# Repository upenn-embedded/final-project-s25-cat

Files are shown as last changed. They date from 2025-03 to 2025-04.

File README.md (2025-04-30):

   Review Assignment Due Date (https://classroom.github.com/a/WXeqVgks)

# final-project-skeleton

* Team Number: 1
* Team Name: CAT
* Team Members: Chekayli Meyer, Andrea González, Taarana Jammula
* GitHub Repository URL: [upenn-embedded/final-project-s25-cat: ese3500s25-final-project-s25-final-project-skeleton created by GitHub Classroom](https://github.com/upenn-embedded/final-project-s25-cat)
* GitHub Pages Website URL: https://upenn-embedded.github.io/final-project-s25-cat/

## Final Project Proposal

### 1. Abstract

*In a few sentences, describe your final project.*

Our final project involves developing an autonomous trash collection vehicle that detects, collects, and stores small lightweight objects while navigating its environment. The robot moves forward until an object is detected within a few centimeters, at which point it stops, collects using a shovel-like part, and pushes it against a wall. The system would use an IR sensor for object detection and an ultrasonic sensor for wall detection.

### 2. Motivation

*What is the problem that you are trying to solve? Why is this project interesting? What is the intended purpose?*

We want to address the growing need for small-scale automated cleanup solutions in both indoor and outdoor environments. We are particularly interested in applying embedded systems and robotics principles to create a functional and modular trash-collection vehicle. This project will allow us to integrate course topics such as sensors, actuator control, serial communication, and embedded C programming in a hands-on and practical setting. Beyond the course requirements, we aim to continue building the system with real-time object recognition and autonomous navigation to explore more advanced robotics applications.

### 3. System Block Diagram

*Show your high level design, as done in WS1 and WS2. What are the critical components in your system? How do they communicate (I2C?, interrupts, ADC, etc.)? What power regulation do you need?*

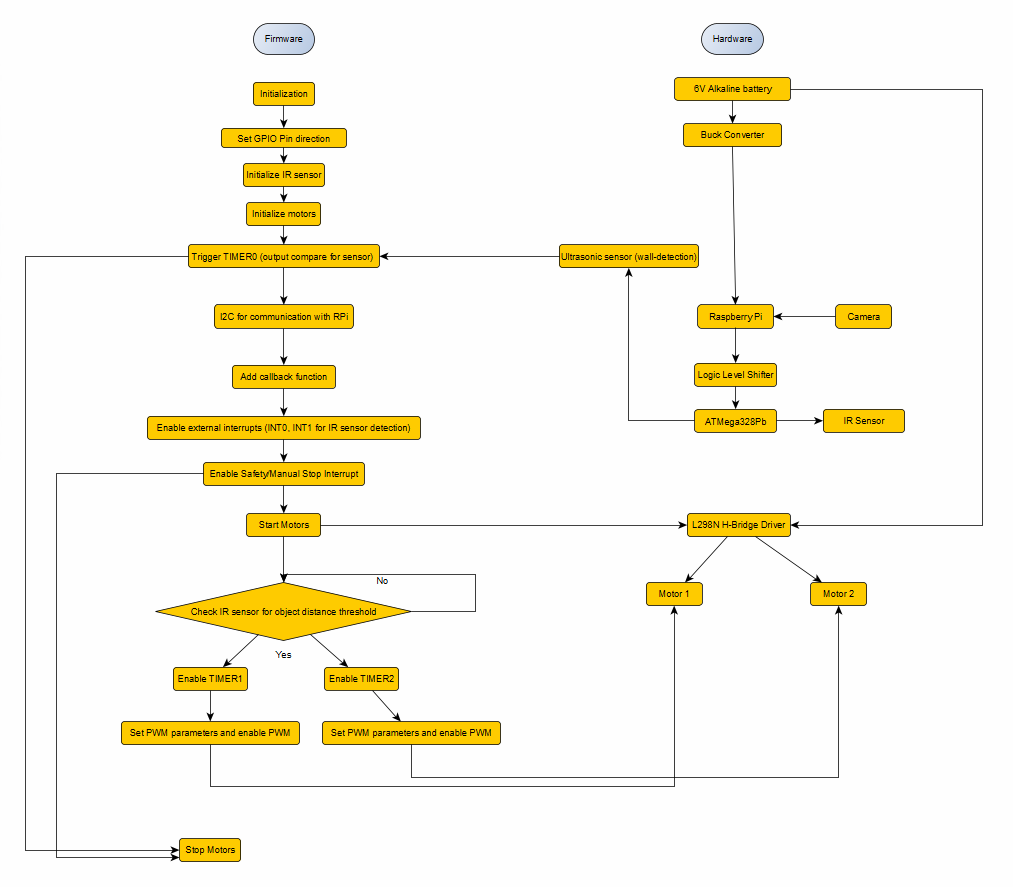
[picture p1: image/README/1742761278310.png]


The critical components of our system are the battery, buck converter, ultrasonic sensor, IR sensor, Raspberry Pi, camera, the ATMega328Pb, the L298N H-Bridge Driver, and 2 motors. The camera will be connected to the raspberry pi and will send information to the ATMega328Pb via I2C (serial communication). Timer0 will use output compare to detect walls, and Timer1 and Timer2 will be connected to separate motors once an object is detected (to push the object to the beacon). Interrupts INT0 and INT1 are used for IR sensor detection for the object. We also added a manual stop interrupt for safety. We have a buck converter from the 6V alkaline battery for power management to the raspberry pi. We also have a logic level shifter between the Raspberry Pi (3.3V) and ATMega328Pb (5V).

### 4. Design Sketches

*What will your project look like? Do you have any critical design features? Will you need any special manufacturing techniques to achieve your vision, like power tools, laser cutting, or 3D printing?*

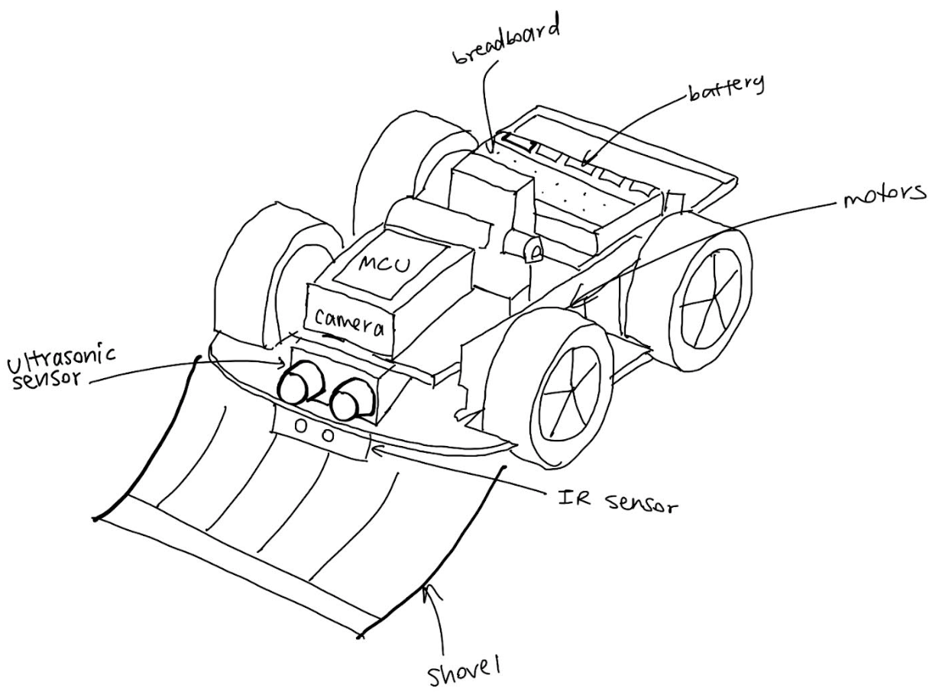
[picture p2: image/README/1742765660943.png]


We are lasercutting the base of the robot car and are purchasing the wheels and other required sensors. The critical design features like motors, a MCU stand, the battery, breadboard, IR sensor, ultrasonic sensor, camera, and shovel are included in the sketch above.

### 5. Software Requirements Specification (SRS)

*Formulate key software requirements here. Think deeply on the design: What must your device do? How will you measure this during validation testing? Create 4 to 8 critical system requirements.*

**5.1 Definitions, Abbreviations**

**ATmega328PB:** Microchip ATmega328PB microcontroller which is an 8-bit AVR MCU

**IR:** Infrared which is the proximity or reflectance sensor

**US:** Ultrasonic Sensor which will be used for distance measurement like in Lab 3

**PWM:** Pulse Width Modulation for motor speed control

**ADC:** Analog-to-Digital Converter

**I2C:** Inter-Integrated Circuit for two-wire serial communication protocol

**GPIO:** General Purpose Input/Output

**5.2 Functionality**

| **Req ID** | **Software Requirement** | **Verification Method** |
| --- | --- | --- |
| **SRS-01** | Sensor Polling Frequency: The firmware will poll the IR sensor and ultrasonic sensor at least 10 times per second (≥10 Hz each) to ensure timely detection of trash and obstacles. | Test: Use a logic analyzer or oscilloscope to verify sensor read operations (or an LED toggled in code on each read) occur at ≥10 Hz. Confirm that both IR and US sensor readings are updated at 100 ms intervals or faster under normal operation. |
| **SRS-02** | Trash Detection Threshold: The system will detect a piece of trash when the IR sensor’s reading exceeds a calibrated threshold value. Upon threshold crossing, the microcontroller shall initiate the trash collection routine (e.g. stop forward motion and activate the scoop) within 100 ms. | Test: Place a standard test object (simulated trash) at the detection range limit (e.g. ~15 cm in front of the IR sensor) and verify that the firmware recognizes it (IR reading above threshold) and triggers the scoop mechanism within 0.1 s. Repeat across several distances and object sizes to confirm reliable threshold detection. |
| **SRS-03** | Obstacle Avoidance Threshold: The firmware will use the ultrasonic sensor to detect walls or obstacles within a set distance (e.g. 30 cm). If an obstacle is closer than the threshold, the system shall halt or turn away within 100 ms to avoid collision. | Test: Gradually bring a wall or large object toward the robot and confirm that when it crosses the ~30 cm range, the robot’s motors stop or turn immediately (within 0.1 s). Use a measuring tape to ensure the trigger distance is ~30 cm and a timer or high-speed camera to measure response time from detection to motor stop. |
| **SRS-04** | Image Processing: The Raspberry Pi will capture images using an attached camera at a rate of at least 1 frame per second while scanning for trash or the beacon. It shall process the image and send detection results to the ATmega328PB via I2C within 500 ms. | Test: Place a target object (trash or beacon) in front of the camera. Verify that the Pi detects it and sends a message to the MCU in under 0.5 seconds. Check Pi logs and I2C communication timing. |
| **SRS-05** | PWM Motor Control Timing: The firmware will drive the motors using a PWM signal of at least 100 Hz frequency (with a target around 500 Hz for smooth control).The duty cycle shall be updated as needed (on speed changes) with a control loop period not greater than 100 ms. This ensures smooth speed variation without perceptible stalling or jitter. | Test: Measure the PWM output on the motor driver input using an oscilloscope. Verify the frequency is ≥100 Hz (e.g. ~500 Hz achieved, within ±5% of target). Change speed commands and confirm the duty cycle adjusts within the next 100 ms cycle. No audible irregularities or excessive motor vibration should be observed at the set frequency (confirm by listening and motor behavior). |
| **SRS-06** | I2C Communication Protocol: The microcontroller will communicate with the Raspberry Pi using the I2C bus operating at standard speed (100 kHz clock). Sensor status updates (e.g. trash detected, weight, obstacle distance) shall be transmitted to the Pi at least 2 times per second, and command/control data from the Pi (e.g. navigation commands) shall be processed within 100 ms of receipt. The I2C communication shall include error-checking (ACK/NACK monitoring); on a communication failure, the system shall retry the transmission at least once within 50 ms. | Test: Use a protocol analyzer or logic analyzer on the I2C lines (with level shifting in place) to verify the bus clock is ~100 kHz. Run the system and confirm via logs that sensor data messages are sent to the Pi ≥2 Hz. Introduce a forced NACK or bus error (e.g. by briefly disconnecting SDA) and ensure the firmware attempts a retry and recovers communication. All commands from the Pi (simulated via I2C commands) should be observed to take effect on the robot (e.g. a movement command causes motor PWM change) within 0.1 s. |
| **SRS-07** | User Interrupt & Safety Response: The system will provide a user interrupt (e.g. an emergency stop button or remote kill switch input to a GPIO interrupt). When the user interrupt is activated, the firmware shall immediately override normal operation and stop all motor activity within 100 ms, entering a safe idle state. Normal operation can only resume after a manual reset or explicit resume command. | Test: While the robot is moving, activate the emergency stop (press the button or trigger the interrupt line). Measure the time for the motors to stop (e.g. using timestamps or an LED triggered at stop); it should be <100 ms. Verify that during the stop condition, no motor motion occurs and the robot remains stationary. Attempt to issue movement commands during the stop state to ensure they are ignored. Finally, reset the interrupt and confirm the system only resumes operation when allowed. |

### 6. Hardware Requirements Specification (HRS)

*Formulate key hardware requirements here. Think deeply on the design: What must your device do? How will you measure this during validation testing? Create 4 to 8 critical system requirements.*

*These must be testable! See the Final Project Manual Appendix for details. Refer to the table below; replace these examples with your own.*

**6.1 Definitions, Abbreviations**

**H-Bridge** An electronic circuit (L298N module) that drives the motors in both directions

**Beacon:** Beacon used as a drop-off location marker

**Battery:** On-board power source (rechargeable) for motors and electronics

**6.2 Functionality**

| **Req ID** | **Hardware Requirement** | **Verification Method** |
| --- | --- | --- |
| **HRS-01** | Drive Motor Performance:The motor and drive system will propel the robot at a forward speed of≥0.3 m/son level ground while carrying a full load of collected trash (at least 2 kg). Each motor (with L298N driver) must provide sufficient torque to start moving from standstill with the full load and climb a mild incline of 5°. | Test: Load the robot with a dummy weight of 2 kg (to simulate trash). Mark a 1 m distance on flat floor and time the robot driving that distance; it should arrive in ≤3.3 s (0.3 m/s or faster). Verify the robot can also ascend a 5° ramp from standstill with the same load without stalling. Monitor motor current draw with an ammeter during these tests to ensure it stays within L298N and motor limits (no overheating or current limiting observed). |
| **HRS-02** | Infrared (IR) Sensor Range & Accuracy: The IR sensor will reliably detect a typical piece of trash (minimum size ~5 cm) at a distance of≥15 cm in front of the robot. Detection reliability at that range should be at least 90% (minimal missed detections under proper conditions). Beyond 15 cm, the sensor should not trigger on the test object, to avoid false positives outside the intended range. | Test: Place a standard test object (e.g. a 5 cm cube or bottle) at 15 cm from the IR sensor and observe the sensor output over 10 trials (approaching and leaving). It should correctly indicate “object present” in at least 9 out of 10 trials at 15 cm. Repeat at slightly greater distances (20 cm, 30 cm) to ensure the sensor does not indicate detection beyond ~15 cm. Also test against different materials/backgrounds to confirm consistent performance and that environmental IR (lighting) does not cause false detection. |
| **HRS-03** | Ultrasonic Sensor Distance & Accuracy:The ultrasonic sensor will measure distances to obstacles in the range of 5 cm up to 300 cm. Within 100 cm, the distance measurement error should not exceed±1 cm , and for longer ranges (up to 300 cm) error should be within ±5 cm . (The sensor’s capability is 2–400 cm with ~0.3 cm precision in ideal conditions) This accuracy is required for reliable wall detection and navigation. | Test: Place a flat obstacle (e.g. a wall or board) at known distances of 10 cm, 50 cm, 100 cm, 200 cm, and 300 cm from the ultrasonic sensor. For each distance, take multiple readings (e.g. 10 samples) and record the measured distances. Calculate the error compared to the true distance – it should be within ±1 cm for ≤100 cm ranges and ±5 cm for the farthest distances. Also verify the sensor consistently detects an object at 300 cm (does not miss it) and that it reports out-of-range when no object is within ~3 m. |
| **HRS-04** | Camera Setup: The forward-facing camera Raspberry Pi Cam V3 will capture images at a resolution of at least 480p and a frame rate of 1 FPS or higher. The camera must be mounted securely and powered from the Raspberry Pi. | Test: Power up the system and verify live image capture at 480p or higher. Confirm the camera stays in place during robot movement and reliably delivers frames to the Pi board for processing.} |
| **HRS-05** | Battery and Power System:The robot will be powered by a battery system that provides sufficient voltage and capacity for both motors and electronics. The battery pack (and regulators) must supply12 V(nominal) for the motors and a regulated5 V±5%for the microcontroller and sensors. The capacity shall support at least1 hourof continuous operation (motors driving and sensors active) before recharge. The 5 V regulator should handle peak current draw (motor drivers + logic, ~2–3 A transient) without the voltage dropping out of the 4.75–5.25 V range. | Test: Use a multimeter to verify the battery voltage and regulator outputs. Under no-load, confirm ~12 V from the battery and 5 V at the logic rail. Then run the robot under a heavy load scenario (e.g. motors stalled or frequent start-stop to draw peak current) and measure the 5 V line stays within 4.75–5.25 V. Check that the system runs for at least 60 minutes on a full charge by driving it continuously in an obstacle course; record the run time until the battery depletes to cutoff. Also observe that the microcontroller and sensors operate normally throughout, indicating the regulator is supplying stable power (no resets or brown-outs). |
| **HRS-06** | Logic Level Interface (I2C Bus Hardware): The I2C level shifter and bus wiring will allow reliable communication between the 5 V ATmega328PB and 3.3 V Raspberry Pi. The hardware must not introduce signal distortion at the standard 100 kHz I2C clock. Pull-up resistors or the level shifter module shall maintain the I2C lines within proper voltage thresholds for both devices. Communication integrity shall be ≥99% (no more than 1% packet loss or corruption during normal operations of 10 minutes). | Test: Instrument the SDA and SCL lines with an oscilloscope while the microcontroller and Pi exchange data. Verify the logic high level on the bus is ~3.3 V (through the level shifter) and rise/fall times are within I2C specifications at 100 kHz. Run a continuous I2C communication test for 10 minutes (transferring hundreds of messages) and count any errors or checksum failures in the data; the error rate should be <1%. Also test the bus in both idle and motor-active scenarios (to ensure motor electrical noise doesn’t disturb signals), checking that communication remains stable (use an EMI filter or shielding if needed to meet this requirement). |

### g7. Bill of Materials (BOM)

*What major components do you need and why? Try to be as specific as possible. Your Hardware & Software Requirements Specifications should inform your component choices.*

*In addition to this written response, copy the Final Project BOM Google Sheet and fill it out with your critical components (think: processors, sensors, actuators). Include the link to your BOM in this section.*

[Link to our BOM](https://docs.google.com/spreadsheets/d/11ymjW0_Uoc0fHEQ4GR5q43txAdh5dIRnGoK7Q-v5SPE/edit?usp=sharing)

ATMega 328PB

This will be our main microntroller that will control the motors and interface between the sensors in real time, and actuate the motors.

Ultrasonic sensor

The ultrasonic sensor will be positioned on top of the vehicle to detect the distance to the nearest wall or large obstacle. This way, we can avoid collisions.

Logic level shifter

Since the digital high of the ATMega328pb and the raspberry pi are different (5 V vs 3.3 V), and we want to communicate through serial, we require a logic level shifter between them. We have chosen a bidirectional logic shifter from adafruit since it will ensure we are able to communicate using I2C.

Infrarred sensor

We have chosen an analog infrarred sensor, since it is more precise than the ultrasonic sensor and it has a longer range than digital infrarred sensors. It will be placed at floor level, facing forward, to detect the "trash" that the vehicle should collect.

Buck converter

We have chosen a buck converter to 5 V because the raspberry pi and ATMega both require a stable 5V input voltage, and the 1.5 V batteries in series can have a voltage of up to 6V. When the batteries can no longer provide a voltage above 5 V, they will be switched for fresh batteries.

Raspberry Pi

The raspberry pi will be used for image processing, and will then send the navigation commands to the ATMega. We will be using this board instead of the ATMega because image processing is very computationally intensive, and we believe that using the ATMega would greatly limit the real-time performance of the system.

Camera

We will use the Raspberry Pi cam v3 because it can interface with the raspberry pi directly. This way, the raspberry pi can do the necessary image processing directly.

Car chassis

To build this, we will design a base board, laser cut it with1/8 inch acrylic and attach the motors on the bottom and the main components.

Wheels

There will be two front wheels, each attached to a motor, and one swivel support wheel in the back. This setup will ensure the vehicle wis stable and had full freedom of movement.

Motor

We have chosen dc gearbox motors motor because we believe they will provide the necessary torque to move the . We will have two motors, one for each of the front wheels that we will be able to actuate independently to steer the car.

Motor driver

The chosen motor driver is able to drive 2 DC motors, at a maximum current of 600 mA per channel. It is compatible with 5 V logic, so I can use the ATMega to control it with PWM output.

Batteries

We have decided to use alkaline AA batteries. This was a decision that balances portability, limitations on lithium-based batteries and weight considerations.

We plan to use 12 batteries in a 4x3 arrangement (4 in series to reach 6V and 3 in parallel). This decision was made to achieve both the voltage and maximum current output required. We have also included battery holders to be able to safely place all the batteries.

### 8. Final Demo Goals

*How will you demonstrate your device on demo day? Will it be strapped to a person, mounted on a bicycle, require outdoor space? Think of any physical, temporal, and other constraints that could affect your planning.*

We will require enough floor space to demonstrate the vehicle moving. We will also require small objects that the system can detect and dispose of.

### 9. Sprint Planning

*You've got limited time to get this project done! How will you plan your sprint milestones? How will you distribute the work within your team? Review the schedule in the final project manual for exact dates.*

| Milestone  | Functionality Achieved | Distribution of Work |
| --- | --- | --- |
| Sprint #1  | We want to finish the lasercutting, attachment, and wiring of the base robot and its connected hardware components. | We will work on this together equally |
| Sprint #2  | We want the robot to be able to move and sense and communicate distances. | We will work on this together equally |
| MVP Demo | We want to be able to perform image processing for trash detection, and correspondingly move the robot to it. | We will work on this together equally |
| Final Demo | We want the robot to have full functionality on sensing and collecting the trash and correspondly moving it to the beacon autonomously. | We will work on this together equally |

**This is the end of the Project Proposal section. The remaining sections will be filled out based on the milestone schedule.**

## Sprint Review #1

### Last week's progress

We gathered most of our materials, including the base robot car, the camera, raspberry pi kit, the NiMH batteries, and the ultrasonic sensor.

We will be using the blue ultrasonic sensor (takes 5V), which we have experienced with the Theremin lab to have a greater range than the green ultrasonic sensor.

Base robot car:



Raspberry Pi Kit:



Batteries & Battery Holder:



For the battery holders, we have sent 2 to print to addlab, to test that they will fit correctly before printing all 8. We are waiting to hear back. This was sent on Monday, so we will consider alternative methods and places to 3D print our components.

For the raspberry pi, we downloaded the RPi OS and made sure to be able to connect the camera. We were able to run a simple opencv script that took a photo with the camera. We have also created a new repository for the raspberry pi code and added it as a submodule to the main project repository. This will allow us to make changes to the code on our own devices, and pull only the relevant changes directly to the Raspberry Pi.

Raspberry Pi setup to computer:



Camera connection:



Raspberry Pi Github Creation:



Addlab Print request for battery holder:



Parts order (IR sensor & Buck Converter):



Shovel design planning:



### Current state of project

* What state is the project in right now?

The project has a great foundational base as we have almost all our hardware components together. We have wired and incorporated the components that we do have. We have begun working on the link between hardware and software through testing with the raspberry pi.

* How the tasks fit into your end goal

We will need all these components to make a functional autonomous trash collection bot. Thus, by acquiring all our parts now, we are able to focus on the wiring connections and the embedded systems part. We also have tested that our raspberry pi is working as expected, which will be fundamental to our image processing.

* Hardware status - have you purchased everything you need (plus backups)? Is everything working right?

We have purchased what we need. We tested out camera and raspberry pi kit, and both work as intended.

### Next week's plan

**Planning**

**Task 1: CADing the shovel then sending to 3D print**

Estimated time: 3 hours + whatever time addlab takes to print (few days)

Assigned team members: Chekayli and Taarana

Definition of done: when it is properly attached to the base robot car

**Task 2: Ensuring the robot can move forward and backward - motor output**

Estimated time: 1 hour

Assigned team members: All

Definition of done: once the robot can move when supplied with power

**Task 3: Start writing firmware for ATMega - sensor input**

Estimated time: 6 hours

Assigned team members: All

Definition of done: once we can serial output actual distance values for the sensors

---

**Future Planning (For preparation of MVP demo and final demo):**

**Task 4: Power routing**

Estimated time: 4 hours

Assigned team members: all

Definition of done: motor and components are powered by the batteries. Dependent on addlab printing time for the battery holders and part arrival time

**Task 5: Interface RPi and ATMega using I2C**

Estimated time: 3-4 hours

Assigned: all

Definition of done: ATMega sends sensor input to RPi, RPi can respond with movement directives.

**Task 6: Object detection using OpenCV**

Estimated time: 6 hours

Assigned: all

Definition of done: we can detect objects to collect successfully from the live video input.

**Task 7: Actually figure out directives for robot movement**

Estimated time: 15 hours

Assigned: all

Definition of done: when the movement of the robot matches the object detection output.

## Sprint Review #2

### Last week's progress

We designed the shovel and an attachment block piece in SolidWorks and sent the parts to print. We designed the shovel piece so that the bottom plate is cut-out, so we can effectively trap and push trash towards the wall. We designed an extruding piece in the center of the cutout, so that we can place the IR sensor or camera to detect objects to pick up. We also created  a slot in the back-plate of the shovel, so we can adjust the height placement of the shovel when attaching it. We split the shovel into 2 halves to fit printing size requirements, and will glue the halves together once they arrive. We are waiting for the main shovel piece to arrive. We designed a block that will fit under the top plate of the base robot car, with a 3mm hole for a screw, that will fit into the slot on the back plate of the shovel (for height adjustment and attachment). We also got the battery holders that fit properly together, printed.

We gathered schematics and documentation relating to the base robot car (KatzBot), and tested the motor control with code, as well as speed and rotation with PWM (higher PWM means greater speeds, also note that there is a minimum PWM of ~100 for the motor to move). We got the car’s wheels to turn forward and backwards separately and simultaneously at different speeds, and the overall car to rotate clockwise.

We expanded upon our code from Part C of the Theremin Lab (Lab 3) and used the HC-SR04P blue ultrasonic sensor (takes 5V), to have a greater distance range than the green ultrasonic sensor. Right now, we have working code that moves the robot towards an object. We were able to serial output distance values for the sensor. Then, we programmed the robot to stop if the ultrasonic sensor reads a smaller distance than our set distance threshold which is adjustable. The robot successfully performs this action. We intend to further test what this threshold will be after implementing the raspberry pi with our robot.

We decided to change our serial protocol from I2C to SPI because we thought we would be able to take advantage of the full-duplex capabilities of the protocol. We are setting the Atmega to be the peripheral and the raspberry pi to be the controller, and we wrote the code to receive SPI commands , and send back either status codes or ultrasonic sensor readings.

We restructured our existing Atmega code to modularize it, since it was all condensed into one file before and it was becoming hard to interpret and find exactly where to change different things.

We wrote the preliminary code for the Raspberry Pi interfacing. Right now, the code handles SPI communication, camera input and object detection*. Next steps involve testing the code.

* everything that would go around the model actually detecting the object.

We also updated the bash script to be able to run the code with SPI, and added more error handling into the setup of the running program.

**Proof:**

Shovel:

shovel

shovel

Printing request:

print

Attachment block for shovel:

shovel

Motor control videos:
[Video 1](https://drive.google.com/file/d/1o-LlPXBNlsq7b0NR9ot6adOTAn2zIAc2/view?usp=sharing)

[Video 2](https://drive.google.com/file/d/1erBPFCrLf8zJfBMNw_j0bJg6JB4yxkOM/view?usp=sharing)

GitHub Commits:

Motor Control:

* [ultrasonic.h] (https://github.com/upenn-embedded/final-project-s25-cat/blob/main/motor_control.c)
* [ultrasonic.c](https://github.com/upenn-embedded/final-project-s25-cat/blob/main/ultrasonic.c)
* [Datasheet](https://github.com/upenn-embedded/final-project-s25-cat/blob/main/datasheets_and_models/Romi%20Mainboard.PDF)

SPI:
[spi.c](https://github.com/upenn-embedded/final-project-s25-cat/blob/main/code/spi.c)

[spi.h](https://github.com/upenn-embedded/final-project-s25-cat/blob/main/code/spi.h)

Raspberry Pi:

[Raspberry Pi repository](https://github.com/andrgv/taaranator_rpi/tree/f2531cf05abb43c9d4bac655ac3ee0facf48a018)



### Current state of project

* What state is the project in right now?

The ultrasonic sensor and motor control of the robot have been thoroughly tested and are working effectively: The robot stops before a collision by tracking if the object in front of it is at a smaller distance than its distance threshold we set. We are working on SPI serial communication with the Raspberry Pi and camera. We are aiming to use image processing to detect trash - we have the IR sensor part in case we would like to incorporate that.

* How the tasks fit into your end goal

From our most recent progress, connecting the hardware and writing the code for the ultrasonic sensor and writing the ATMega code for the motor control allows us to move the robot car towards the wall and stop before collision. For the image processing component, we are leveraging the Raspberry Pi and Camera and are figuring out SPI to detect what is trash and what is not. This is to differentiate between whether we should “collide” into the object in question or stop (indicating a wall nearby).

* Hardware status - have you purchased everything you need (plus backups)? Is everything working right?

We have purchased what we need. We tested our camera, raspberry pi kit, base robot car, and ultrasonic sensor, and everything works as intended.

### Next week's plan

**Reflection on Last Week’s Planning:**

For Task 1 (CADing the shovel then sending to 3D print), we estimated 3 hours; however, this took around 7-8 hours given that we further familiarized ourselves with Solidworks for the applications we were aiming to implement. Also, Addlab asked us to resize components a few times before printing given that they first said we could have a 16x10x10in build size; however, later asked us to do 10x10x10in, hence we had to pivot our dimensions to account for this.

For Task 2 (Ensuring the robot can move forward and backward - motor output), we estimated 1 hour; however, due to the complexity of our robot and its datasheets, we took 4 hours to implement the motor control (moving wheels in different directions and speeds) with the hardware and software in a cohesive manner.

For Task 3 (Start writing firmware for ATMega - sensor input), we estimated 6 hours; however, this task only took us 3 hours to implement such that the robot stopped once the ultrasonic sensor read a small distance in front of it - smaller than that of our set distance threshold. We were able to serial output actual distance values for the sensors, using base code from the Theremin lab.

**Future Planning:**

*Task 4: Power routing*

Estimated time: 4 hours

Assigned team members: Andrea (soldering), All (connection to robot car)

Definition of done: soldering wires out of the battery holders and connecting the batteries to the robot car

*Task 5: Interface RPi and ATMega using SPI*

In hindsight, I am no longer sure the change in protocol was a great idea because the ATMega is very limited with pins and timers, and we are constrained by the motors and ultrasonic sensor requiring timers to function. We will figure out how to/if we can use timer 3, and in the worst case scenario rewrite the serial communication to do I2C. Our next steps will be to test and debug the code we wrote on the ATMega and Raspberry Pi to make sure that it does work.

Estimated time: 3-4 hours

Assigned: Andrea

Definition of done: Figuring out how to use 4 assigned pins and rewire motor control PWM as needed. The ATMega needs to sends sensor input to RPi, RPi can respond with movement directives.

*Task 6: Object detection using OpenCV*

Next steps include actually making a model for trash detection. We are currently considering a few different options:

1. Take many pictures and build a model. Pros: will probably more accurate for our intention. Cons: Data collection will take time. Training and adjusting will potentially also take time. Note: could take some existing model as a base.
2. Filter by color. Pros: potentially faster. Cons: processing might not be as reliable. Different lighting conditions might introduce issues into the system.
3. Using a pretrained model. Pros: faster deployment. Cons: don’t know where to find a suitable one. Might not be very accurate for our usecase

Estimated time: 6 hours

Assigned: All

Definition of done: we can detect objects to collect successfully from the live camera input.

*Task 7: Figure out directives for robot movement*

Estimated time: 15 hours

Assigned: All

Definition of done: when the movement of the robot matches the object detection output.

## MVP Demo

1. Show a system block diagram & explain the hardware implementation.

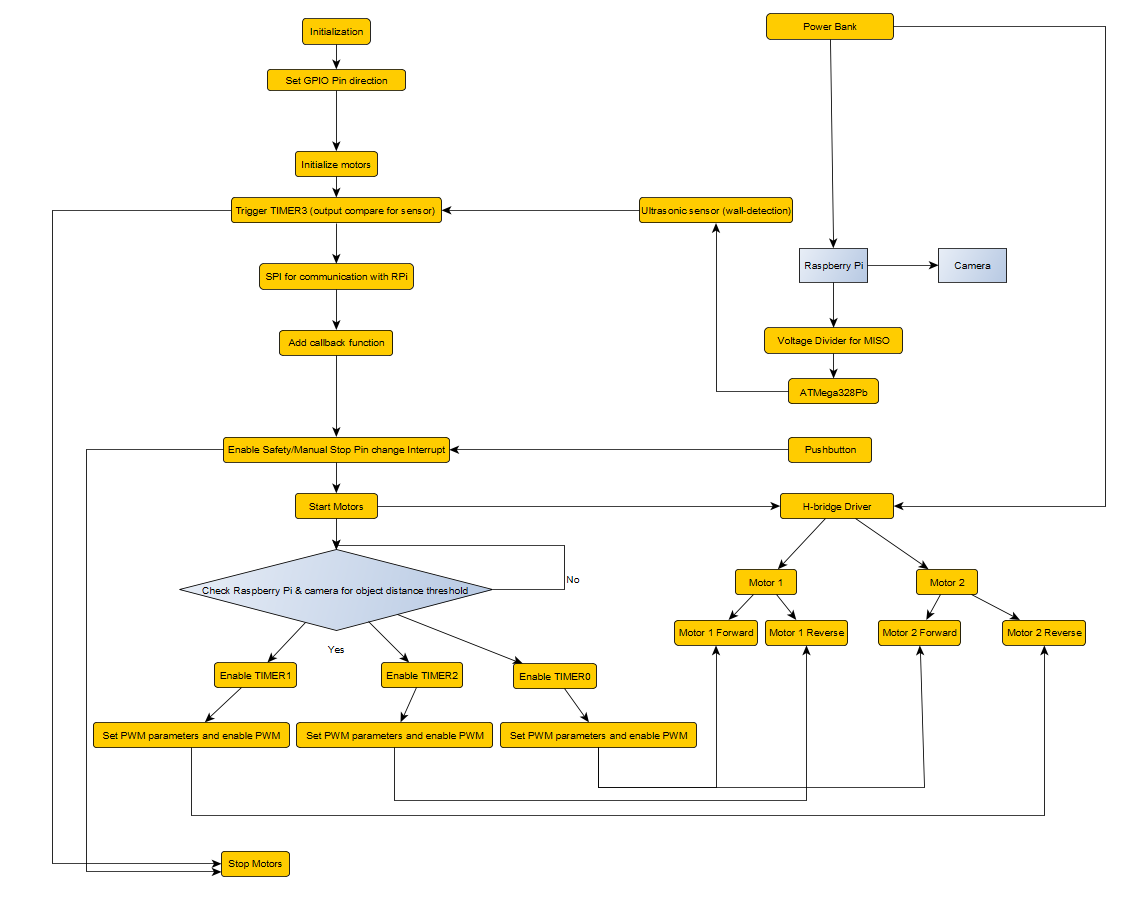
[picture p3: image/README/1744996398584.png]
   

   NOTE: The blue blocks in the above System Block diagram correspond to component we have not yet intergrated for our MVP demo, but plan to incorporate for our final demo.

   The critical components of our system for the MVP demo are the ultrasonic sensor, Raspberry Pi, camera, the ATMega328Pb. The L298N H-Bridge Driver and 2 motors were provided with the base robot car (Katzbot).

   Right now, we have the raspberry pi connected to the AtMega328Pb where the Raspberry Pi will send signals to the AtMega328Pb via SPI serial communication. We are preloading directions into the Raspberry Pi for MVP demo purposes. The ultrasonic sensor will use Timer3 for output compare to detect objects close to it, but eventually we want to use it to detect walls, while the camera and raspberry pi will detect the objects (we plan to train a model and use image processing). Timer0 is connected to motor 1 forward and motor 2 forward, Timer2 was used for motor1 reverse, and Timer1 was used for motor2 reverse. Eventually, once the object is detected, the motors will be activated to push the object to the beacon/wall. We are using a pin change interrupt for a manual safety stop through a push-button. We have a power bank to power the Raspberry Pi. We also have a voltage divider between the Raspberry Pi (3.3V) and ATMega328Pb (5V).

The main requirements we are currently hitting are Timers (PWM with motors), interrupts (pin change interrupt with a push button for emergency stop). We plan to incorporate image processing for the final demo.

2. Explain your firmware implementation, including application logic and critical drivers you've written.

   We have our code modularized such that we have files for the motor control, ultrasonic sensor, and SPI communication protocol handled separately which we integrate all together in our main file. We made the corresponding header files for these.

   For the motor control, we are implementing timers 0,1,2 and initializing them. Then we case depending on the specific type of direction we need, forward, right, left, back, counterclockwise rotation, clockwise rotation, and stop (or break) which is based upon the motor specification of the datasheet from the robot frame we are using.

   For the ultrasonic sensor, we have a function that will trigger the sensor, and use a timer-based interrupt to receive the echo and calculate the distance in cm from the number of ticks.

   For the SPI, we have implemented the ATMega to be a peripheral of the Raspberry Pi controller. We have implemented this using polling instead of an SPI interrupt. This decision was made with the idea of leaving the ATMega listening for SPI communication most of the time, while not interfering with the in-order traversal of the steps in main. The ATMega receives the movement command from the Raspberry Pi as a char, which it will later interpret, and sends back the latest distance reading to the ATMega.

   We also have a pin change interrupt ISR for the hard emergency stop button within the main file.

   In our main function, we first initialize all the sensors, pins, timers and enable global interrputs. Then we enter our execution loop, where we measure the distance (by calling the ultrasonic.c measureDistance and storing it). If the distance is less than 20 cm, we brake. Otherwise, we start listening for the next incoming message from SPI, and set the MISO message to be the latest measurement. Once we receive the command from MOSI, we case on the value of the command character and call the corresponding functions to move the motors. If at any point during this loop we press the emergency brake button, we set off the pin change interrupt, which will set the emergency_stop flag variable to 1. Then we will exit the execution loop, brake the robot and enter an infinite idle loop.

   We have the uart protocol that we were given in class, but we have only used it so far for debugging purposes. We do not plan on using uart for any further functionality.
3. Demo your device.
   Demo completed
4. Have you achieved some or all of your Software Requirements Specification (SRS)?

   We have achieve some of our software requirements. Some of these requirements have been modified since we are no longer using the infrarred sensor (SRS-01, SRS-02) and have substituted the I2C communication for SPI (SRS-02, SRS-06)

   SRS-01: Sensor polling frequency. The polling frequency of the ultrasonic sensor depends on the frequency of command sending from the Raspberry Pi to the ATMega, since we are measuring the distance once per main loop cycle. Right now, the subprocess to measure a new distance takes less than 100 ms, so we can and have achieved the target 10 Hz frequency in our testing process. We have decided that it will take unnecessary time and power to be measuring as often, when it won't be sent back to the raspberry pi.

   SRS-02: Trash Detection Threshold. This software requirement has been modified since we are no longer using the infrarred sensor. We are planning on detect trash with the camera connected to the raspberry pi. This is a software requirement that will be developed in the following week, and is tied to the image processing and recognition model.

   SRS-03: Obstacle avoidance threshold. We have achieved this objective. The robot stops when the ultrasonic sensor detects a distance of less than 20cm from the nearest object.

   SRS-04: Image Processing. We have not fully achieved this software requirement yet since we haven't implemented the image processing capabilities yet. Wre have also changed the Raspberry Pi-ATMega communication protocol from I2C to SPI to have fast full-duplex communication.

   SRS-05: PWM Motor Control. We have achieved this software requirement. We have tested different PWM outputs and have settled  for 7.81 KHz for the PWM frequency as the most appropriate.

   SRS-06: I2C Communication protocol. This software requirement has been modified to SPI communication protocol. We have achieved this software requirement since we are able to send commands from the Raspberry Pi to the ATMega, which the ATMega interprets and sets the motor direction. Then the ATMega returns the last distance measured by the ultrasonic sensor.

   1. Show how you collected data and the outcomes.

   SRS-01: For the polling frequency, we ran the code for the ultrasonic sensor freely and we observed it was meeting our frequency specifications.

   SRS-03: In the MVP demo we demonstrated how the robot would stop when it would detect an object at less than 20 cm, and resume movement when it no longer detected the obstacle.

   SRS-05: We tested the PWM output with the oscilloscope at the start of the development. Now we have the working motors demonstratd in the MVP demo.

   SRS-06: Raspberry Pi & AtMega328Pb communication via SPI

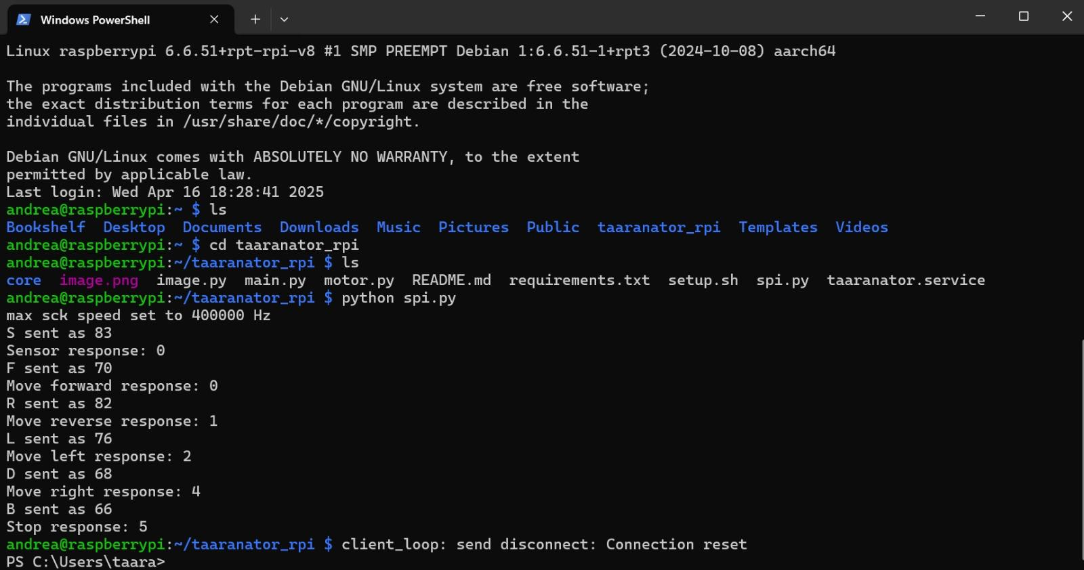
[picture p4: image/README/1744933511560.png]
   
5. Have you achieved some or all of your Hardware Requirements Specification (HRS)?

   We have acheived all of our Hardware Requirements except image processing with the raspberry pi that integrates with the ATMega. We have SPI working with dummy direction data to communicate between the Raspberry Pi and AtMega. We have the ultrasonic sensor working properly to detect objects at a certain distance threshold. Later, we will use the ultrasonic sensor for wall detection, while the camera will detect trash. Our robot's motors are working properly and move based on the directions we input. Note that we no longer need the IR sensor and the buck converter as we are using image processing to detect objects and a powerbank to power the raspberry pi and a voltbetween the Atmega328PB and Raspberry PI.

   1. Show how you collected data and the outcomes.

      We tested the ultrasonic sensor code that integrates Timer 3 and used the serial terminal to print out distance values:

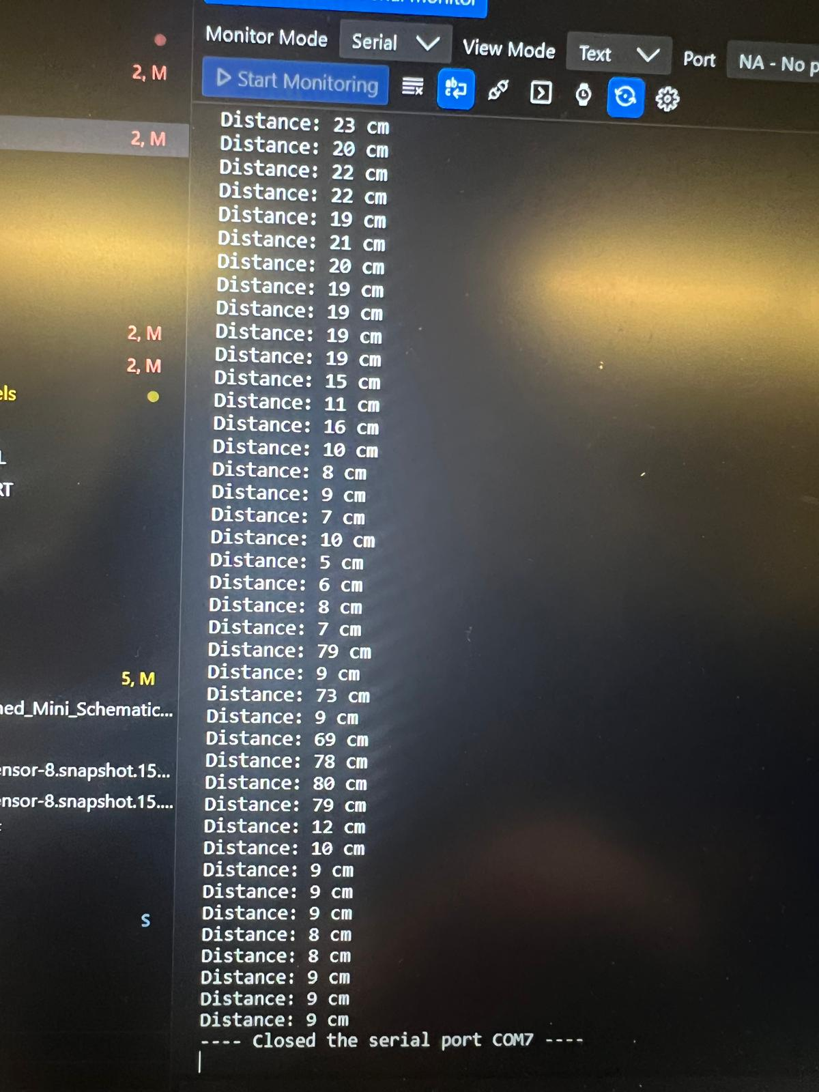
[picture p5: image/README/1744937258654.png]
      

   Video Link: https://drive.google.com/file/d/17VDj15f5mGnT_kkAiv49TOgbWERdB4tv/view?usp=drivesdk
6. Show off the remaining elements that will make your project whole: mechanical casework, supporting graphical user interface (GUI), web portal, etc.

   We have a shovel 3D printed and attached. It has a slot and holes drilled within such that we were able to  connect it to the mainframe of the robot with tight zipties. We also  We  ave an open bottom plate with barriers to "trap" trash and we have a ledge in between to mount ultrasonic, which we already have mounted, and enough space to mount the camera next.

   For the processing and command transmission, we connect the raspberry pi to the internet, which allows us to remotely shell into the device and execute the python script. This is currently only required to start, since the robot should be autonomous. We plan for the robot to be truly autonomous by configuring the Raspberry Pi to automatically execute the Python control script on boot using systemd. We currently have a bash script that will set this up for us, along with initializing the relevant interfaces (SSH and SPI) and downloading and updating the necessary libraries.

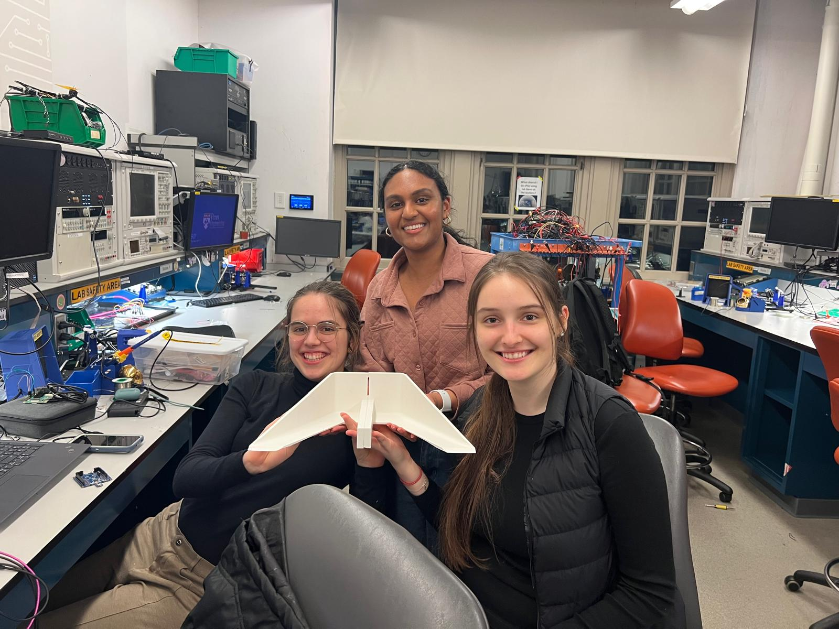
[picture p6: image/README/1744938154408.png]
   

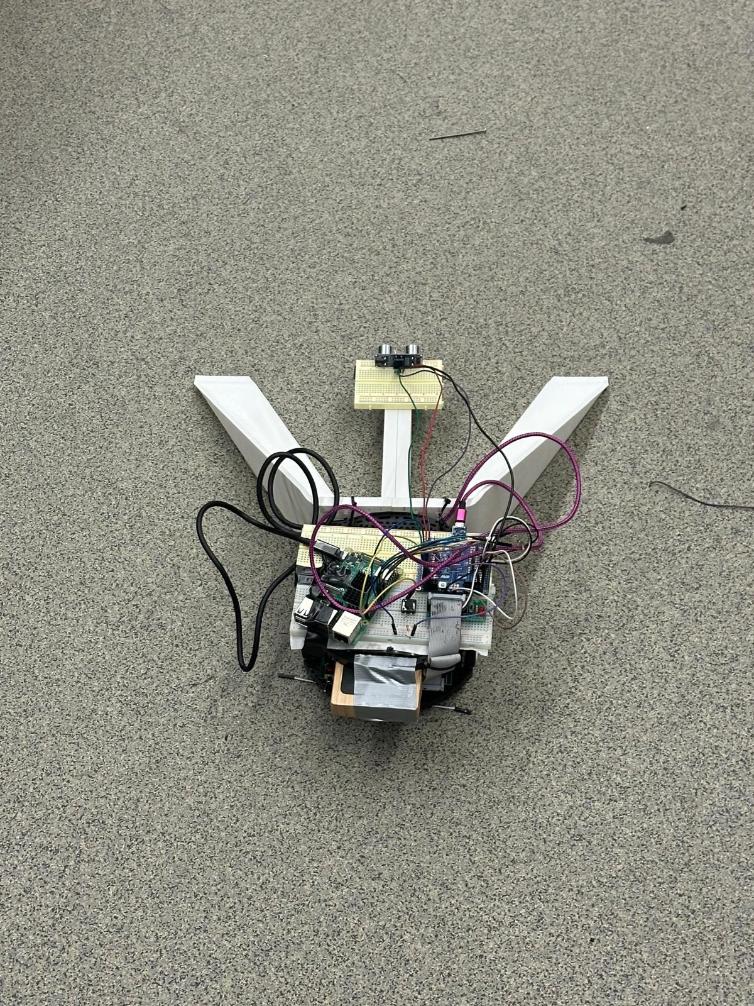
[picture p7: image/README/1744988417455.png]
   

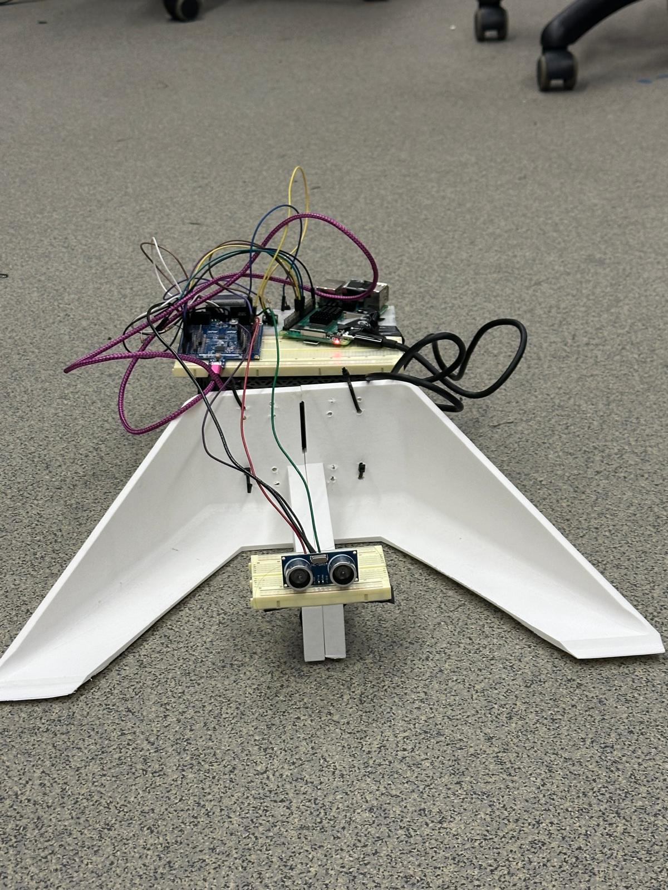
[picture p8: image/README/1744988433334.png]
   
7. What is the riskiest part remaining of your project?

   The riskiest part remaining of our project is the integration of the image processing via the raspberry pi. Alongside with this, we must intelligently decide how best to train the model to detect an object we are defining as trash, while minimizing processing compute. After this works, the remaining risk lies in the raspberry pi's ability to correctly send steering commands to the ATMega to detect, collect and drop-off the trash.

   1. How do you plan to de-risk this?

   We are using a yellow block to simulate trash. This will simplify our machine learning training of the data as the dimensions of the block will be consistent. The trash the robot is aiming to collect is for relatively similar sized, smaller objects. We will also be using a pretrained model as a base for the image recognition. To de-risk this model training as much as we can, we will use as much data needed to minimize the loss function. This data will take the form of pictures of the "trash" taken with the camera we will be using on our final system. This will allow the model to be as fine-tuned to our hardware as possible.
8. What questions or help do you need from the teaching team?

   One question which has surfaced for our team is how may we improve the grip of our wheels or lighten the load of the robot as the wheels sometimes lose contact with the ground, slowing the pace of our robot due to mechanics and physicals, not due to the embedded system. To address this, we added a rock to center the mass such that there is greater contact between the wheels and ground; however, we encounter the wheels do not always remain in contact with the ground.

## Final Project Report

[You can find our final project report here!](https://upenn-embedded.github.io/final-project-s25-cat/)

### 1. Video

[Final video](https://drive.google.com/file/d/1tgKRL_t79QS1e0g7a95CM60AKaz--BF2/view?usp=sharing)

* The video must demonstrate your key functionality.
* The video must be 5 minutes or less.
* Ensure your video link is accessible to the teaching team. Unlisted YouTube videos or Google Drive uploads with SEAS account access work well.
* Points will be removed if the audio quality is poor - say, if you filmed your video in a noisy electrical engineering lab.

### 2. Images

[Insert final project images here]

*Include photos of your device from a few angles. If you have a casework, show both the exterior and interior (where the good EE bits are!).*

### 3. Results

*What were your results? Namely, what was the final solution/design to your problem?*

#### 3.1 Software Requirements Specification (SRS) Results

*Based on your quantified system performance, comment on how you achieved or fell short of your expected requirements.*

*Did your requirements change? If so, why? Failing to meet a requirement is acceptable; understanding the reason why is critical!*

*Validate at least two requirements, showing how you tested and your proof of work (videos, images, logic analyzer/oscilloscope captures, etc.).*

| ID | Description | Validation Outcome |
| --- | --- | --- |
| SRS-01 | Sensor Polling Frequency (Updated): Instead of polling, we implemented timer-based interrupts for the ultrasonic sensor, using timer 3. The system behavior confirmed that wall detection was responsive without lag. | Confirmed, wall detection was responsive without lag during testing with timer-based interrupts. |
| SRS-02 | Trash Detection (Updated): We replaced the IR sensor with a YOLO machine learning model running on the Raspberry Pi. In testing, the robot reliably detected yellow blocks placed within view of the camera and triggered collection behavior appropriately. | Verified, robot successfully detected yellow blocks and triggered collection behavior during real-world tests. [▶ Watch our camera detecting the block video](https://drive.google.com/file/d/1n4UYuvp0TMSXZDLKCUhrddrH8jbGPYtZ/view?usp=sharing) |
| SRS-03 | Obstacle Avoidance Threshold: Wall detection using the ultrasonic sensor remained as planned. We manually validated behavior by observing that the robot stopped moving when approaching walls within about 20–30 cm. | Confirmed, robot stopped within the expected range when approaching walls, verified through manual tests. |
| SRS-04 | Image Processing (Updated): The Raspberry Pi captured and processed images at approximately 1 frame per second. We observed that the robot responded to trash detection reliably. | Verified, robot processed images and responded to trash detection with no significant delay. [▶ Watch our camera perceiving distance of the block video](https://drive.google.com/file/d/12GPv1BvtwwBkfn28_EqNGDv7AikHxlrk/view?usp=sharing) |
| SRS-05 | PWM Motor Control Timing: Motor PWM control was implemented with Timer0 at a target of ~500 Hz. We observed smooth and consistent motor operation without perceptible jitter. | Confirmed, motor control was smooth with no perceptible jitter during operation. [▶ Watch our motor control (forward, backwards, speed) video](https://drive.google.com/file/d/1o-LlPXBNlsq7b0NR9ot6adOTAn2zIAc2/view?usp=sharing) |
| SRS-06 | SPI Communication Protocol (Updated): Instead of I2C, we implemented SPI communication between the Raspberry Pi and ATMega328PB for transmitting navigation directions. We confirmed low-latency updates from detection to motor action. | Verified, SPI communication provided low-latency updates from detection to motor action during tests. **SPI Dummy Value Test** SPI Dummy Value test |
| SRS-07 | User Interrupt & Safety Response: An emergency stop button connected to PC0 was successfully integrated using a pin-change interrupt. During testing, the motors stopped within 100 ms of button press, as confirmed by manual tests. | Confirmed, motors stopped within 100 ms of button press during manual safety tests. [▶ Watch our motor rotation video](https://drive.google.com/file/d/1erBPFCrLf8zJfBMNw_j0bJg6JB4yxkOM/view?usp=sharing) |

**Confusion Matrix Normalized - Prequantized Model**  
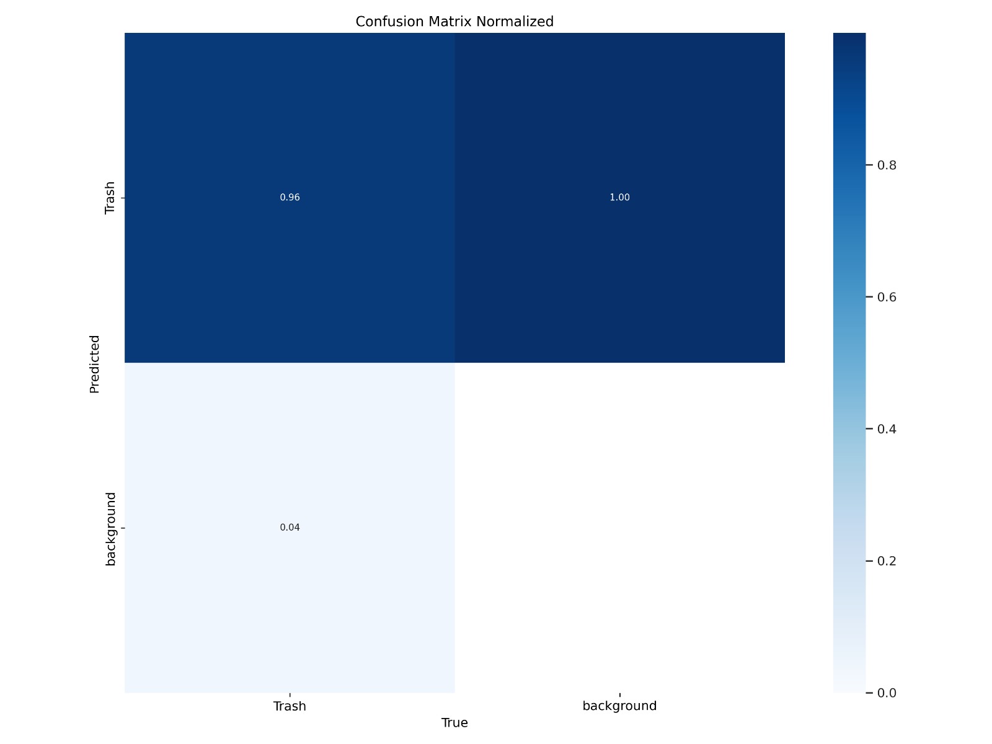
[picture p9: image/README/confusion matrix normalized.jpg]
Confusion Matrix Normalized - prequantized model


**Composite of Images - Prequantized Model**  
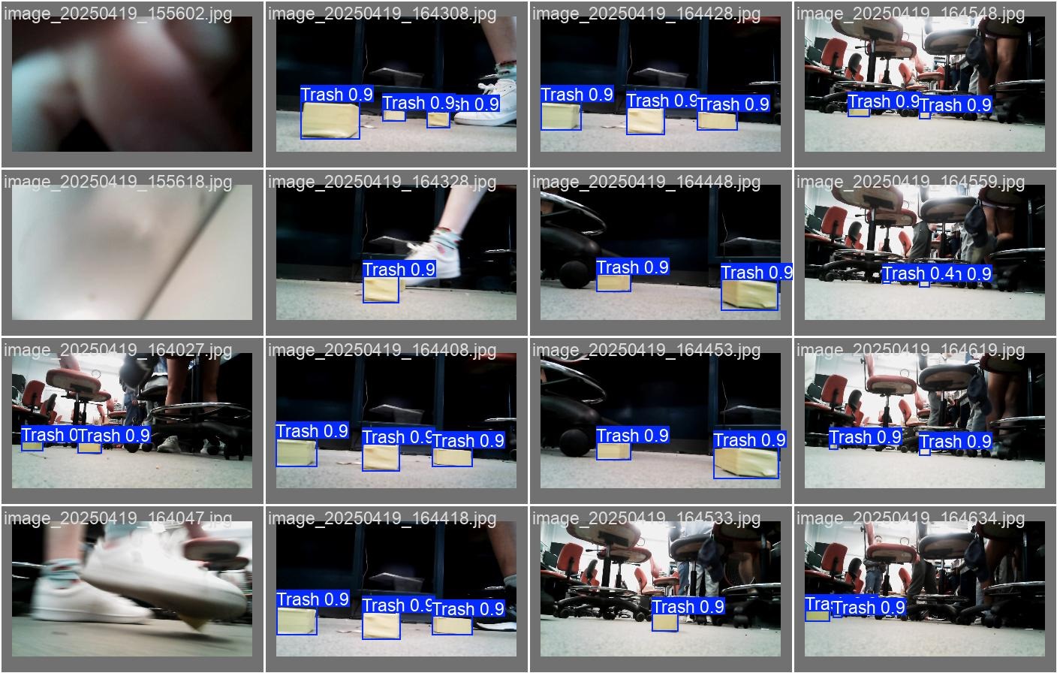
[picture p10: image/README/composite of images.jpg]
Composite of images - prequantized model


#### 3.2 Hardware Requirements Specification (HRS) Results

*Based on your quantified system performance, comment on how you achieved or fell short of your expected requirements.*

*Did your requirements change? If so, why? Failing to meet a requirement is acceptable; understanding the reason why is critical!*

*Validate at least two requirements, showing how you tested and your proof of work (videos, images, logic analyzer/oscilloscope captures, etc.).*

| ID | Description | Validation Outcome |
| --- | --- | --- |
| HRS-01 | Drive Motor Performance: The robot was able to drive forward while carrying a load. Although ramp testing was not conducted, the motors provided sufficient torque for smooth motion and start-up. A counterweight at the back successfully balanced the front shovel. We validated speed across 1 meter and observed no stalling or overheating. | Verified, the robot was able to move smoothly, with no stalling or overheating, during speed tests across 1 meter. |
| HRS-02 | Trash Detection via Camera instead of IR Sensor (Updated): We did not use an IR sensor. Instead, we used a forward-facing Raspberry Pi camera paired with a YOLO machine learning model to detect trash objects. The camera reliably identified yellow blocks placed in the robot’s path and triggered collection behavior accordingly. Detection performance was stable across multiple trials and lighting conditions. | Verified, YOLO model on the Raspberry Pi successfully detected trash in various lighting conditions. [▶ Watch our camera detecting the block video](https://drive.google.com/file/d/1n4UYuvp0TMSXZDLKCUhrddrH8jbGPYtZ/view?usp=sharing) |
| HRS-03 | Ultrasonic Sensor Distance & Accuracy: We placed obstacles at 10 cm, 50 cm, 100 cm, 200 cm, and 300 cm and recorded 10 readings at each distance. Measurement error was within ±1 cm for short range and ±5 cm for long range. The sensor consistently detected objects up to 3 meters without false negatives. | Verified, ultrasonic sensor showed consistent distance accuracy with minimal error and reliably detected objects up to 3 meters. |
| HRS-04 | Camera Setup: The Arducam was mounted securely and delivered live image captures at ≥480p resolution and 1 FPS. The camera remained stable during movement, and frame delivery to the Pi was confirmed during trash detection testing. | Confirmed, the camera delivered stable images at 480p resolution and maintained stable operation during testing. |
| HRS-05 | Battery and Power System: A power bank was used to supply the required motor and 5 V logic rails. Under high load, the 5 V line remained within 4.75–5.25 V, and no brown-outs or instability were observed. The robot ran continuously for at least 2 hours, exceeding the 1-hour requirement. | Verified, the robot successfully ran for over 2 hours under continuous load with stable voltage. |
| HRS-06 | Logic Level Interface (SPI Bus Hardware): SPI communication between the 5 V ATMega328PB and 3.3 V Raspberry Pi was implemented using a voltage divider. Oscilloscope readings showed clean signal transitions, and extended communication tests confirmed stability and accuracy without significant packet loss, even under motor noise. | Confirmed, SPI communication remained stable and accurate with no significant packet loss during testing. **SPI Dummy Value Test** SPI Dummy Value test |
                                                                                                                      |

### 4. Conclusion

Reflect on your project. Some questions to address:

* **What did we learn from it?** We learned how to integrate subsystems such as motor control, SPI communication, ultrasonic sensing, and computer vision into a single working platform. We also gained experience troubleshooting hardware-level issues like voltage mismatches and adapting quickly when components did not perform as expected.
* **What went well?** Motor control, SPI communication, and extended robot operation went very smoothly after setup. Our robot consistently detected objects using the camera and moved appropriately. We were able to successfully run the robot for long periods without brown-outs or crashes.
* **What accomplishments are we proud of?** We are proud of successfully transitioning from using an IR sensor to a camera-based machine learning model for trash detection. We are also proud of implementing SPI communication using a voltage divider when our logic level shifter failed, and ensuring the robot was mechanically stable and robust during long-term testing.
* **What did we learn/gain from this experience?** We gained valuable hands-on experience integrating hardware and software, troubleshooting electrical issues, and building systems that are reliable over time. We also developed stronger problem-solving skills by adjusting our approach when real-world conditions differed from expectations.
* **Did we have to change our approach?** Yes. We changed from using an IR sensor to a camera for trash detection, switched from I2C to SPI communication for robustness, and replaced the 6V battery and buck converter setup with a simpler power bank solution. We also added a counterweight to balance the front-heavy design caused by the shovel.
* **What could have been done differently?** We could have tested critical components like the level shifter and power system independently before integration. We also could have fine-tuned the software for ultrasonic distance measurement to improve accuracy and consistency. Adding additional ultrasonic sensors positioned at angles would have improved wall detection when approaching at non-head-on angles.
* **Did we encounter obstacles that we didn’t anticipate?** Yes. We did not anticipate the failure of the logic level shifter, which required building a voltage divider ourselves. We also did not initially plan for the shovel’s front-heavy impact on the robot’s balance, which required a counterweight solution.
* **What could be a next step for this project?** Next steps could include improving the ultrasonic sensor software to filter noise and calibrate distances more precisely, as well as adding additional ultrasonic sensors at angles to improve obstacle detection and wall following when approaching walls from different directions.

## References

Fill in your references here as you work on your final project. Describe any libraries used here.
- [ATMega 328PB datasheet](https://ww1.microchip.com/downloads/aemDocuments/documents/MCU08/ProductDocuments/DataSheets/40001906C.pdf)
- [ATmega328PB Xplained Mini Schematics](https://github.com/upenn-embedded/final-project-s25-cat/blob/main/datasheets_and_models/ATmega328PB_Xplained_Mini_Schematics.pdf)
- [KatzBot Datasheets](https://github.com/upenn-embedded/final-project-s25-cat/blob/b537aac7de03d78fe197f5bd12d081c1ee69fa79/datasheets_and_models/Romi%20Mainboard.PDF)
- [Ultrasonic Sensor Documentation](https://github.com/upenn-embedded/final-project-s25-cat/blob/8c9b48332c07fcebf3f4ddfdd915e39affeacde0/datasheets_and_models/hc-sr04-ultrasonic-sensor-8.snapshot.15.z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)
- [Raspberry Pi 4 Model B](https://datasheets.raspberrypi.com/rpi4/raspberry-pi-4-datasheet.pdf)
- [Raspberry Pi OS](https://www.raspberrypi.com/software/)
- [Ultralytics YOLOv5 documentation](https://github.com/ultralytics/yolov5)
- [OpenCV Python documentation](https://pypi.org/project/opencv-python/)
- [ONNX Runtime documentation](https://onnxruntime.ai/)
- [Python Spidev documentation](https://pypi.org/project/spidev/)
- [Numpy documentation](https://numpy.org/)

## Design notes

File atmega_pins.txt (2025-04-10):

Motor: (modified pins)
PD6: Right motor forward, PWM timer0
PD3: Right motor reverse, PWM timer2
PD5: Left motor forward, PWM timer0
PB1: Left motor reverse, PWM timer1

Ultrasonic:
PD4, PB0

SPI:
PB4: MISO
PB3: MOSI
PB5: SCK
PB2: CS

Motor pins were changed because PB2 is reserved for CS in SPI

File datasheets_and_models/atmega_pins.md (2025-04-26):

# Debrief of the pins

## VERY IMPORTANT!!!!!!! disconnect all jumpers from ATMega328pb before flashing code to it

## Aspirational assignments

### Motor

PD6: Right motor forward, PWM timer0 OC0A

PD3: Right motor reverse, PWM timer2 OC2B

PD5: Left motor forward, PWM timer0 OC0B

PB1: Left motor reverse, PWM timer1 OC1A

PC0 : Emergency stop

### Ultrasonic sensor

PD4: Trig pin
PE2: Echo pin, timer 3 ICP3 input capture

### SPI

Using SPI0

PB4: MISO - green, white
PB3: MOSI - yellow
PB5: SCK - blue
PB2: CS - purple

## Current assignments - broken and I believe actually not true

### Motor: (modified pins)

PD6: Right motor forward, PWM timer0
PD3: Right motor reverse, PWM timer2
PD5: Left motor forward, PWM timer0
PB1: Left motor reverse, PWM timer1

### Ultrasonic sensor

PD4: Trig pin
PB0: Echo pin, timer 3

### SPI

PB4: MISO
PB3: MOSI
PB5: SCK
PB2: CS

Motor pins were changed because PB2 is reserved for CS in SPI

## Original assignments

### Motor

PB2: Right forward, PWM timer1

PD6: Right reverse, PWM timer0

PB1: Left forward, PWM timer1

PD5:  Left reverse, PWM timer0

### Ultrasonic sensor

**PD4**: TRIG_PIN

**PB0**: ECHO_PIN, timer1

## What the datasheet says

### SPI

The ATMega has SPI0 and SPI1!

#### SPI0

PB4: MISO0

PB3: MOSI0

PB5: SCK0

PB2: SS0 (chip select)

#### SPI1

PC0: MISO1

PE3: MOSI1

PC1: SCK1

PE2: SS1 (chip select)

### Timers

#### Timer0

16-bit

PD4: T0

PD6: OC0A

PD5: OC0B

#### Timer1

16-bit

PD5: T1

PB1: OC1A

PB2: OC1B

PB0: ICP1

#### Timer2

8-bit async

PB3: OC2A

PD3: OC2B

#### Timer3

// TODO data sheet mentions external counter input for both tc3 and tc4. look into that

16-bit

PE3: T3

PD0: OC3A

PD2: OC3B

PE2: ICP3

#### Timer4

16-bit

PE1: T4

PD1: OC4A

PD2: OC4B // TODO: wdym timer3 and 4 share pins for OC_B ;-;. See table 17-10 for reference. can both timers be used at the same time without weird mode changing or multipllexing (if even possible)?

PE0: ICP4

### Screenshots for reference

#### Section 4

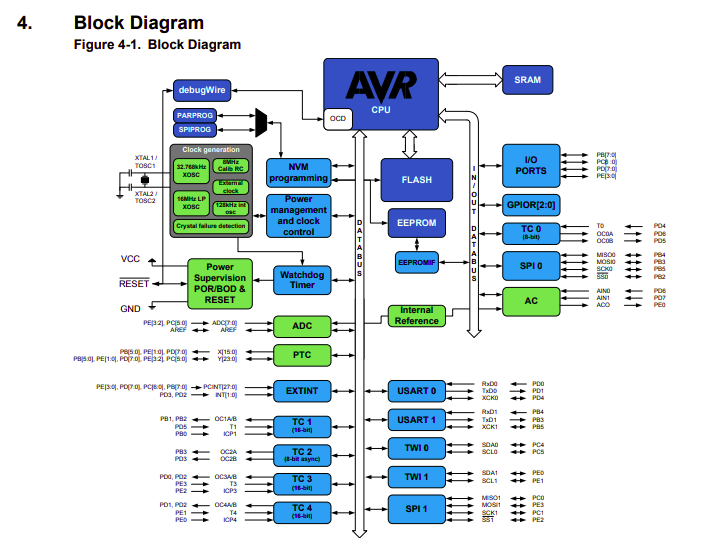
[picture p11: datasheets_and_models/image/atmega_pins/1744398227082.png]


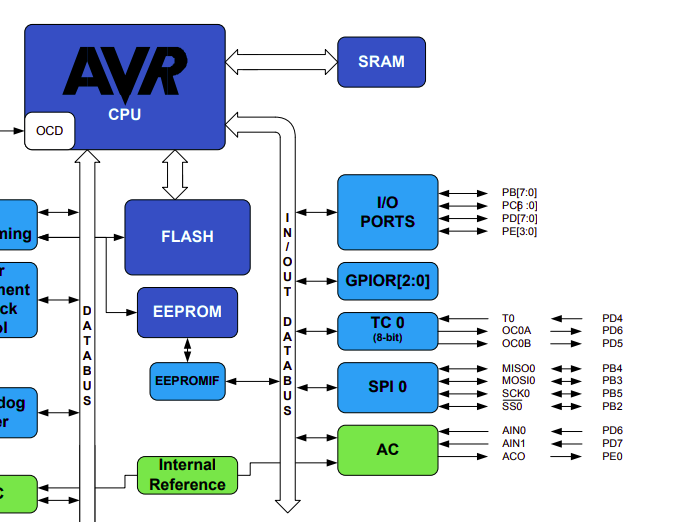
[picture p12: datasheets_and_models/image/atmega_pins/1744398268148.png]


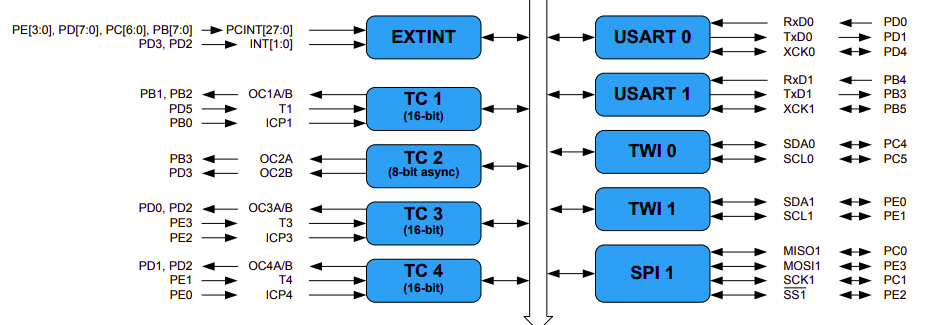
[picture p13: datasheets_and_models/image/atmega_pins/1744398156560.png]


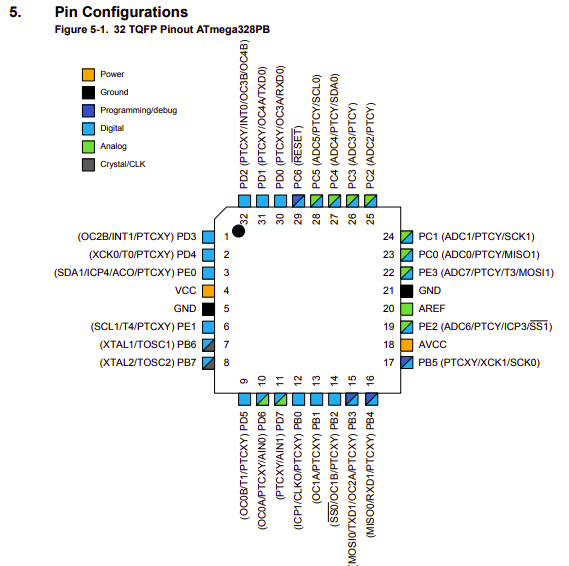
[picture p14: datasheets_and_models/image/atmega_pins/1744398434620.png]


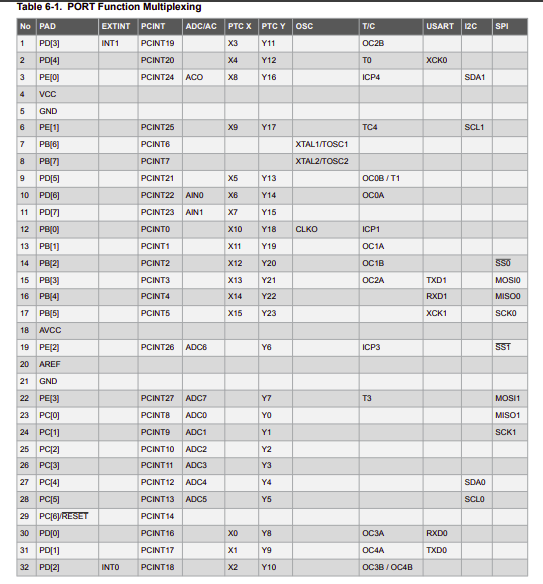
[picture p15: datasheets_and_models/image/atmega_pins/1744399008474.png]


#### Section 17

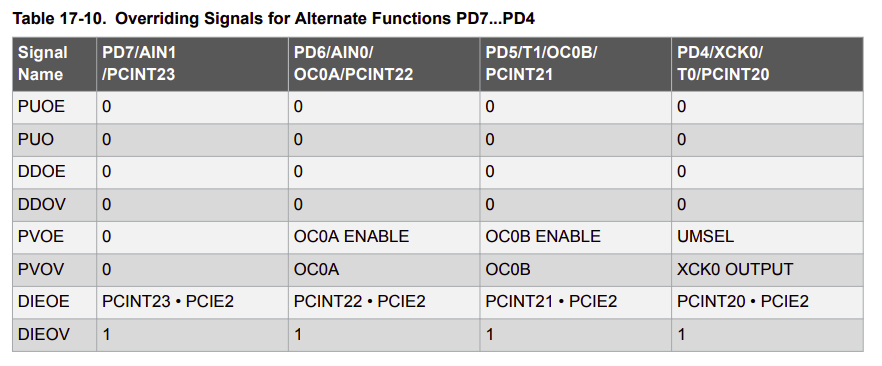
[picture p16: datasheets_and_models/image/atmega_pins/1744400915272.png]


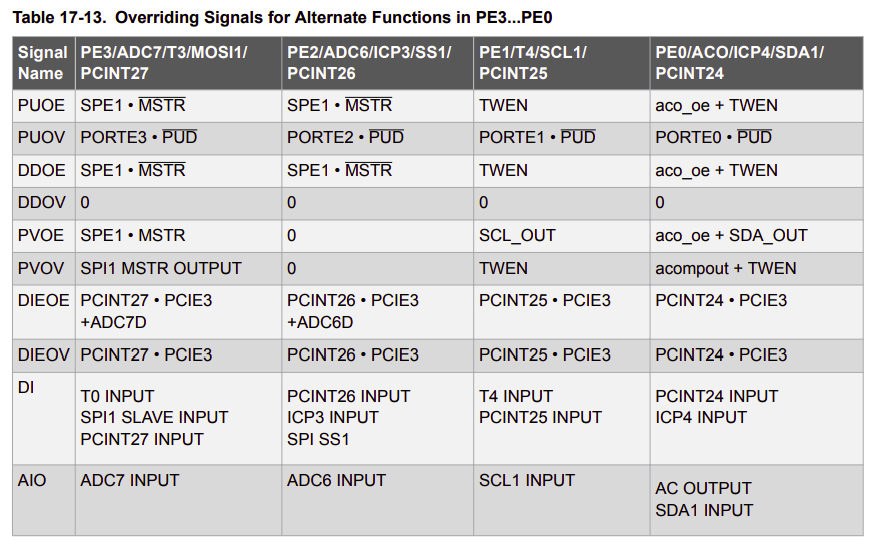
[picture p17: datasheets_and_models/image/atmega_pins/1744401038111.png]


#### Section 18

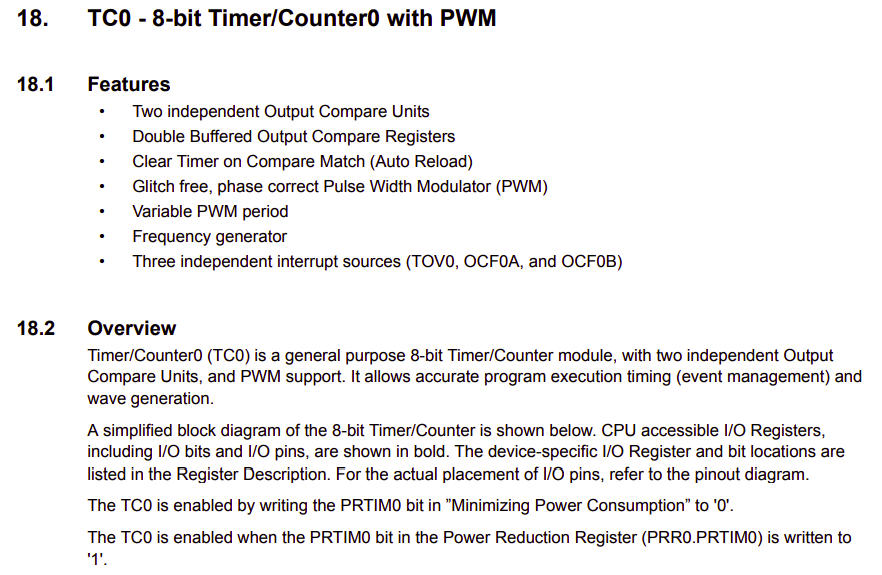
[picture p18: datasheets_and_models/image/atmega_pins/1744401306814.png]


#### Section 35

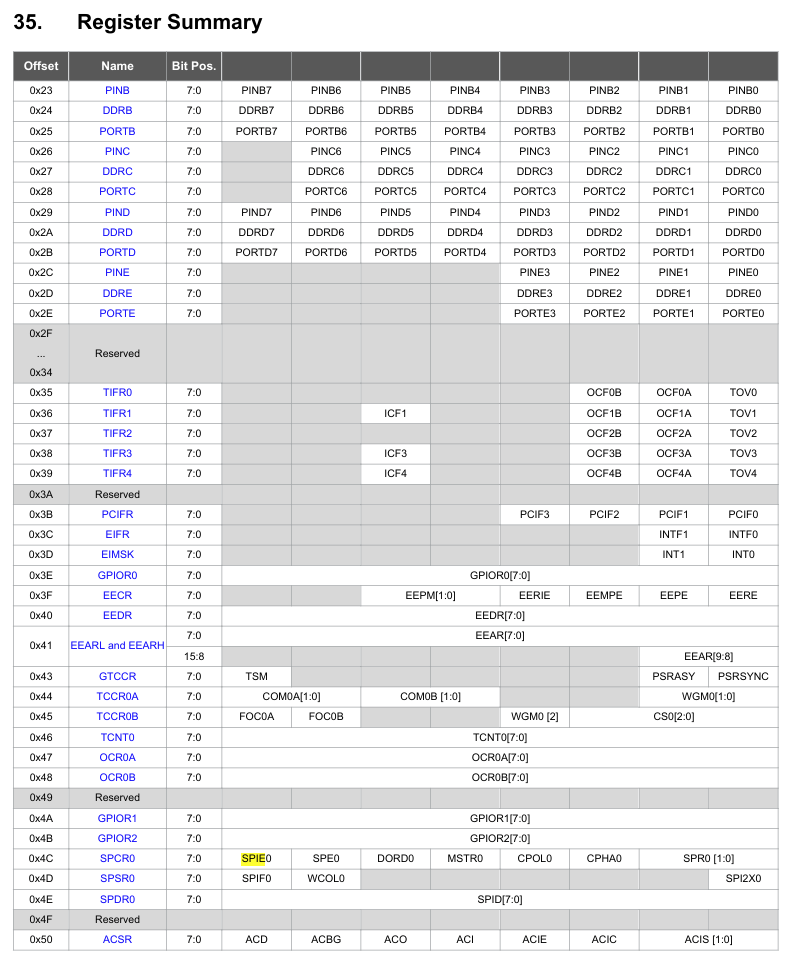
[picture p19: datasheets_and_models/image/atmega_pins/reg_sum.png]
35. Register Summary


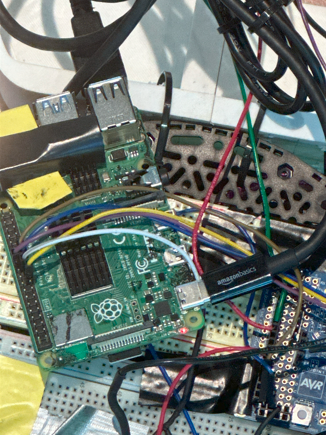
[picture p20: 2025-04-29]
image/README/rpi.png

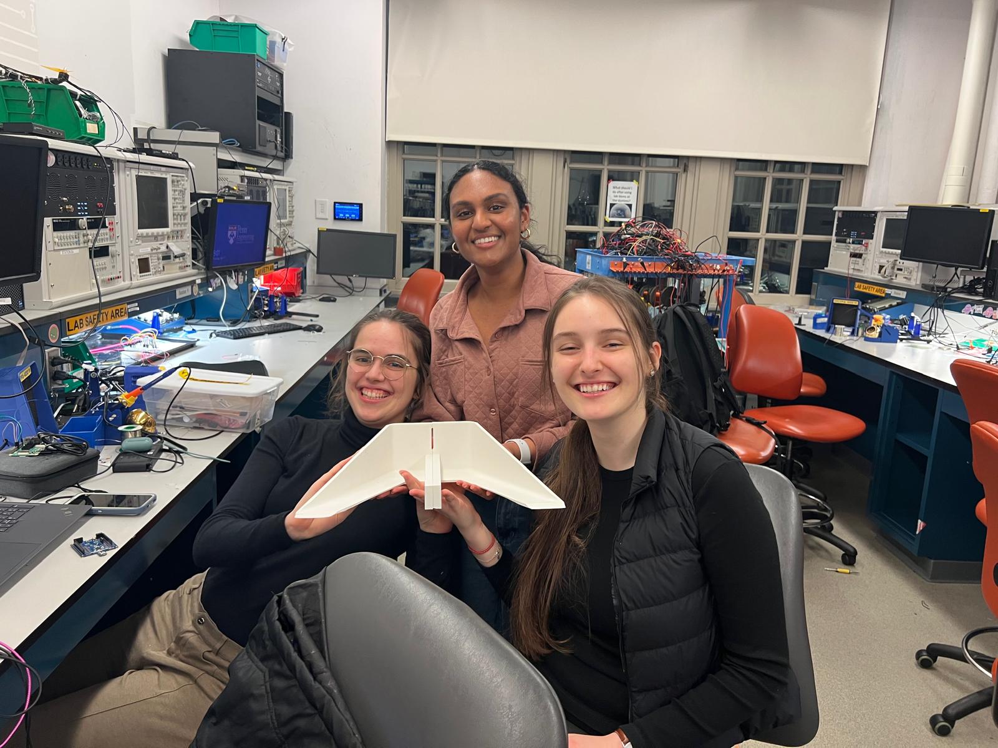
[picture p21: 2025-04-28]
image/README/WhatsApp Image 2025-04-28 at 12.37.47_ce98078c.jpg

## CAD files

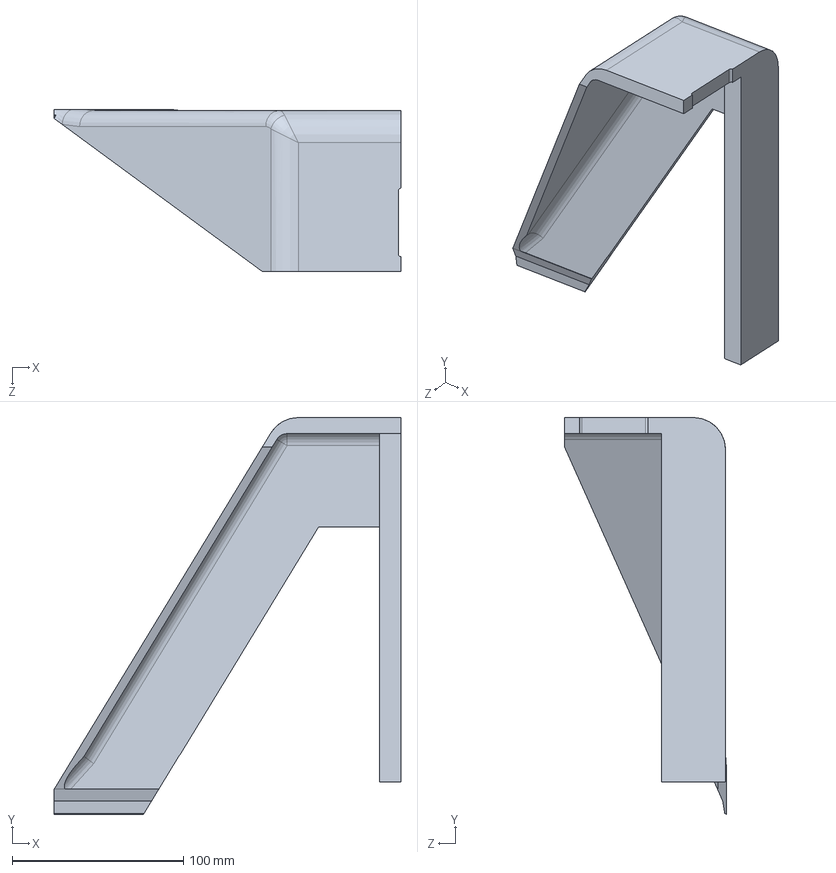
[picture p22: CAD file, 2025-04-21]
datasheets_and_models/3dprints/ShovelHalf2.SLDPRT
202.7 x 232.0 x 94.6 mm

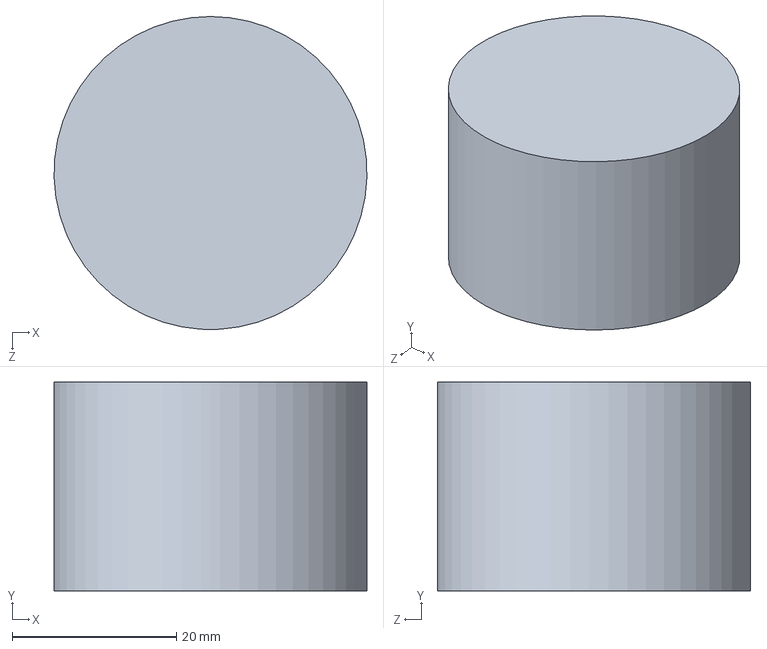
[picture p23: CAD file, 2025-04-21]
datasheets_and_models/3dprints/cylinder.SLDPRT
38.1 x 25.4 x 38.1 mm

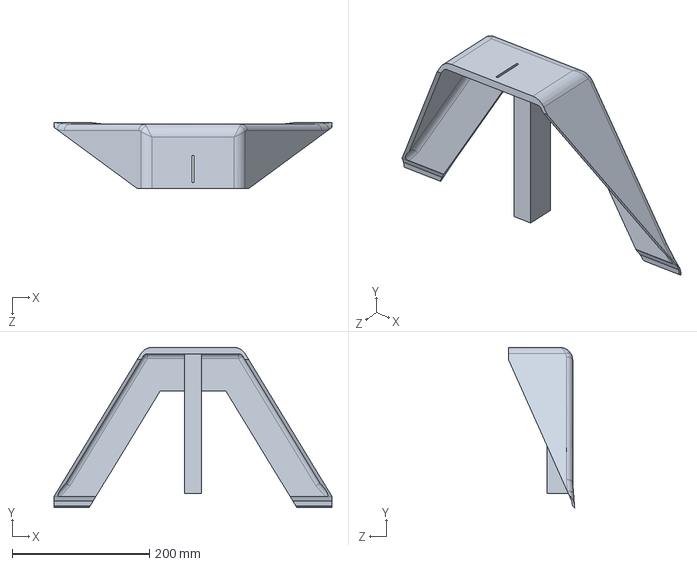
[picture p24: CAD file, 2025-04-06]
datasheets_and_models/3dprints/Shovel_v2.SLDPRT
405.5 x 233.5 x 96.8 mm

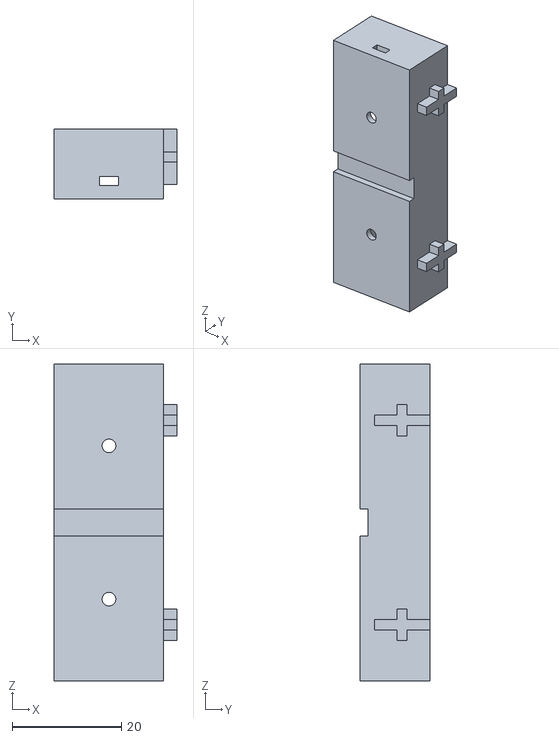
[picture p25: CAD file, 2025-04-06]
datasheets_and_models/3dprints/battery_slots_v2.STL
22.4 x 12.8 x 57.9

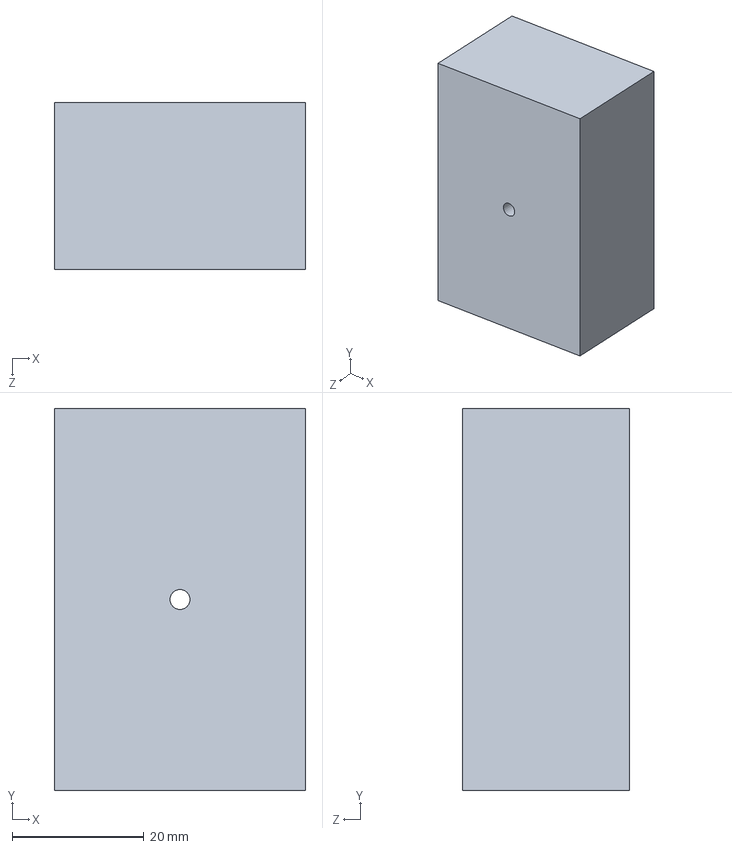
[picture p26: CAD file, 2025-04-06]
datasheets_and_models/3dprints/block.SLDPRT
38.1 x 57.9 x 25.4 mm

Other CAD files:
datasheets_and_models/holders/holder_v5.DWG
datasheets_and_models/3dprints/ShovelHalf1.SLDPRT
datasheets_and_models/holders/holder_v4.SLDPRT
datasheets_and_models/holders/cam_holder_v3.SLDPRT
datasheets_and_models/3dprints/agvarela_ese3500_cylinder_prusamini.STL
datasheets_and_models/holders/camera_holder.SLDPRT
datasheets_and_models/3dprints/battery_slots.SLDPRT
datasheets_and_models/holders/camera_holder_feet.SLDPRT
datasheets_and_models/holders/holder_v3.DWG
datasheets_and_models/holders/holder_v2.SLDPRT
datasheets_and_models/holders/cam_holder_v2.SLDPRT
datasheets_and_models/3dprints/Shovel_v2.STL
datasheets_and_models/3dprints/block.STL
datasheets_and_models/holders/cam_holder_v2.DWG
datasheets_and_models/holders/cam_holder_v3.DWG
datasheets_and_models/holders/camera_holder.DWG
datasheets_and_models/holders/camera_holder_feet.DWG
datasheets_and_models/holders/holder_v2.DWG
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

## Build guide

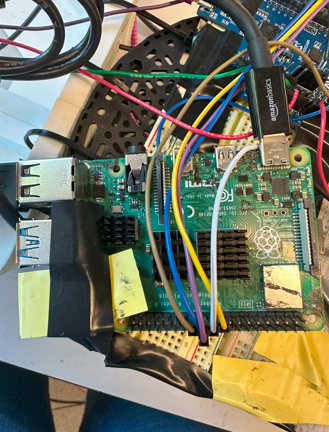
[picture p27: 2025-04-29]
image/README/Raspberry Pi Wiring.png

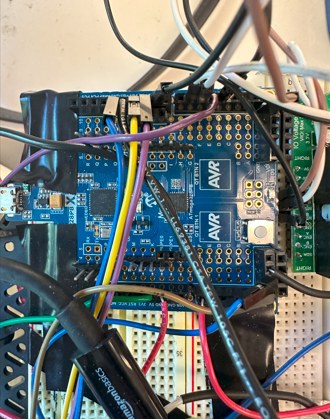
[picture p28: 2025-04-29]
image/README/ATMega Wiring.png

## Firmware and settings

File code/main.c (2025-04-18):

#ifndef F_CPU
#define F_CPU 16000000UL
#endif

#include <avr/io.h>
#include <avr/interrupt.h>
#include "motor_control.h"
#include "spi.h"
#include "ultrasonic.h"
#include <util/delay.h>
#include "uart.h"
#include <stdio.h>

// -------- CONFIG --------
#define SPEED 500
#define DELAY 1000

#define BUTTON_PIN_REG PINC
#define BUTTON_BIT PC0
#define BUTTON_PCINT PCINT8  // PC0 maps to PCINT8

volatile uint8_t emergency_stop = 0;

// -------- EMERGENCY STOP BUTTON INIT --------
void pin_change_interrupt_init() {
    DDRC &= ~(1 << BUTTON_BIT);     // Set as input
    PORTC |= (1 << BUTTON_BIT);     // Enable pull-up

    PCICR |= (1 << PCIE1);                // Enable PCINT[14:8] group
    PCMSK1 |= (1 << BUTTON_PCINT);        // Enable PC0
}

ISR(PCINT1_vect) {
    _delay_ms(10); // debounce
    if (!(BUTTON_PIN_REG & (1 << BUTTON_BIT))) {
        emergency_stop = 1;
    }
}

// -------- MAIN --------
int main(void) {
    uint8_t meas = 0;

    // Init subsystems
    uart_init();

    spiInit();
    motorInit();
    ultrasonic_timer3_init();
    pin_change_interrupt_init();

    sei();

    while (!emergency_stop) {
        measureDistance();          // Triggers measurement
        meas = getDistance();       // Gets last measured distance
        if (meas < 20) {
            brake();
        } else {
            char insn = SPI_Recv(meas); // receive command
            switch (insn) {
                case 'F':
                    forward(SPEED);
                    break;
                case 'B':
                    reverse(SPEED);
                    break;
                case 'L':
                    ccw_rotation(SPEED);
                    break;
                case 'R':
                    cw_rotation(SPEED);
                    break;
                case 'S':
                    brake();
                    break;
                case 'D':
                    break;
                default:
                    brake();
                    break;
            }
        } 
    }
    brake();
    printf("EMERGENCY STOP triggered!\n");
    emergency_stop = 1;
    for(;;);

    return 0;
}

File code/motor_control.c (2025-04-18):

#include <stdio.h>
#include <stdlib.h>
#include <avr/interrupt.h>
#include <avr/io.h>
#include <util/delay.h>
#include "motor_control.h"

void motorInit() {
    timer0_init();
    timer1_init();
    timer2_init();
}

// ----- TIMER INITIALIZATIONS -----
void timer0_init(void) {
    DDRD |= (1 << L_F) | (1 << R_F);
    TCCR0A = (1 << WGM00) | (1 << WGM01); // fast PWM
    TCCR0B = (1 << CS01); // prescale by 8
}

void timer1_init(void) {
    DDRB |= (1 << L_R); // Set left-reverse motor as output
    TCCR1A = (1 << WGM10) | (1 << COM1A1); // Fast PWM, OC1A
    TCCR1B = (1 << WGM12) | (1 << CS11); // Fast PWM
}

void timer2_init(void) {
    DDRD |= (1 << R_R);
    TCCR2A = (1 << WGM20) | (1 << WGM21);
    TCCR2B = (1 << CS21);
    OCR2B = 0;
}

// ----- PWM CONTROL HELPERS -----
void enable_pwm_IN1(void) {
    TCCR0A |= (1 << COM0A1);
    TCCR0A |= (1 << COM0B1);
}

void disable_pwm_IN1(void) {
    TCCR0A &= ~(1 << COM0A1);
    TCCR0A &= ~(1 << COM0B1);
}

void enable_pwm_IN2_left(void) {
    TCCR1A |= (1 << COM1A1);
}

void disable_pwm_IN2_left(void) {
    TCCR1A &= ~(1 << COM1A1);
}

void enable_pwm_IN2_right(void) {
    TCCR2A |= (1 << COM2B1);
}

void disable_pwm_IN2_right(void) {
    TCCR2A &= ~(1 << COM2B1);
}

// ----- MOTOR CONTROL -----
void forward_right(uint8_t speed) {
    disable_pwm_IN2_right();
    DDRD |= (1 << PD3);
    PORTD &= ~(1 << PD3);
    
    TCCR0A |= (1 << COM0A1);
    OCR0A = speed;
}

void reverse_right(uint8_t speed) {
    TCCR0A &= ~(1 << COM0A1);
    DDRD |= (1 << PD6);
    PORTD &= ~(1 << PD6);
    
    enable_pwm_IN2_right();
    OCR2B = speed;
}

void brake_right(void) {
    disable_pwm_IN1();
    disable_pwm_IN2_right();
    
    DDRD |= (1 << PD6) | (1 << PD3);
    PORTD |= (1 << PD6) | (1 << PD3);
}

void forward_left(uint8_t speed) {
    disable_pwm_IN2_left();
    DDRB |= (1 << PB1);
    PORTB &= ~(1 << PB1);

    TCCR0A |= (1 << COM0B1);
    OCR0B = speed;
}

void reverse_left(uint8_t speed) {
    TCCR0A &= ~(1 << COM0B1);
    DDRD |= (1 << PD5);
    PORTD &= ~(1 << PD5);
    
    enable_pwm_IN2_left();
    OCR1A = speed;
}

void brake_left(void) {
    disable_pwm_IN1();
    disable_pwm_IN2_left();

    DDRD |= (1 << PD5);
    DDRB |= (1 << PB1);
    PORTD |= (1 << PD5);
    PORTB |= (1 << PB1);
}

// Combined motor control functions

void forward(uint8_t speed) {
    forward_left(speed);
    forward_right(speed);
}

void reverse(uint8_t speed) {
    reverse_left(speed);
    reverse_right(speed);
}

void brake(void) {
    brake_left();
    brake_right();
}

void cw_rotation(uint8_t speed) {
    forward_left(speed);
    reverse_right(speed);
}

void ccw_rotation(uint8_t speed) {
    forward_right(speed);
    reverse_left(speed);
}

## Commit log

2025-03-23 flowchart and design sketch
2025-03-23 Partial BOM
2025-03-23 included BOM link
2025-04-06 update parts and datasheets
    [Shovel_v2.SLDPRT, Shovel_v2.STL, battery_slots.SLDPRT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]
2025-04-06 motor control
2025-04-07 ultrasonic sensor with movement control code
2025-04-10 added spi stuff, in the middle of modifying code to compartmentalize and make different components work together
2025-04-12 partial reference material for the timer in the atmega
2025-04-14 Chekayli's testing new pin assignments
2025-04-16 motors work
2025-04-16 spi sends and responds, but actual info is wrong
    [spi.c]
2025-04-16 update pin docs
2025-04-16 office hours ask spi
2025-04-16 spi works
2025-04-16 ultrasonic with polling
2025-04-17 ultrasonic and emergency push added to main
2025-04-17 push button interrupt pin
2025-04-17 push button brake in main
2025-04-17 Flowchart updated
2025-04-17 Flowchart explanation started
2025-04-18 ultrasonic by itself
2025-04-19 Add camera holder CAD
    [camera_holder.DWG, camera_holder.SLDPRT, camera_holder_feet.DWG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]
2025-04-19 CAD shovel designs
    [ShovelHalf1.SLDPRT, ShovelHalf2.SLDPRT]
2025-04-21 add more models
    [agvarela_ese3500_cylinder_prusamini.STL, cam_holder_v2.DWG, cam_holder_v2.SLDPRT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]
2025-04-24 v3 cam holder
    [holder_v2.SLDPRT, holder_v3.DWG]
2025-04-24 add screw holes to cam holder
    [cam_holder_v3.DWG, cam_holder_v3.SLDPRT]
2025-04-24 add v4 holder
    [holder_v4.DWG, holder_v4.SLDPRT]
2025-04-26 website template
    [cam_holder_v3.SLDPRT, camera_holder.DWG, camera_holder.SLDPRT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]
